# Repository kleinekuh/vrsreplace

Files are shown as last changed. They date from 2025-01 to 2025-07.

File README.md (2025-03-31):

# VRS Replace
This „simple“ project (circuit & software) is a replacement for my old Vaillant VRS auroMATIC 560 thermal solar control. Other VRS auroMATIC systems operating with VR10 / VR11 sensors, should also work. Furhter it's possible using the control for warm water heating only (C1/C2).

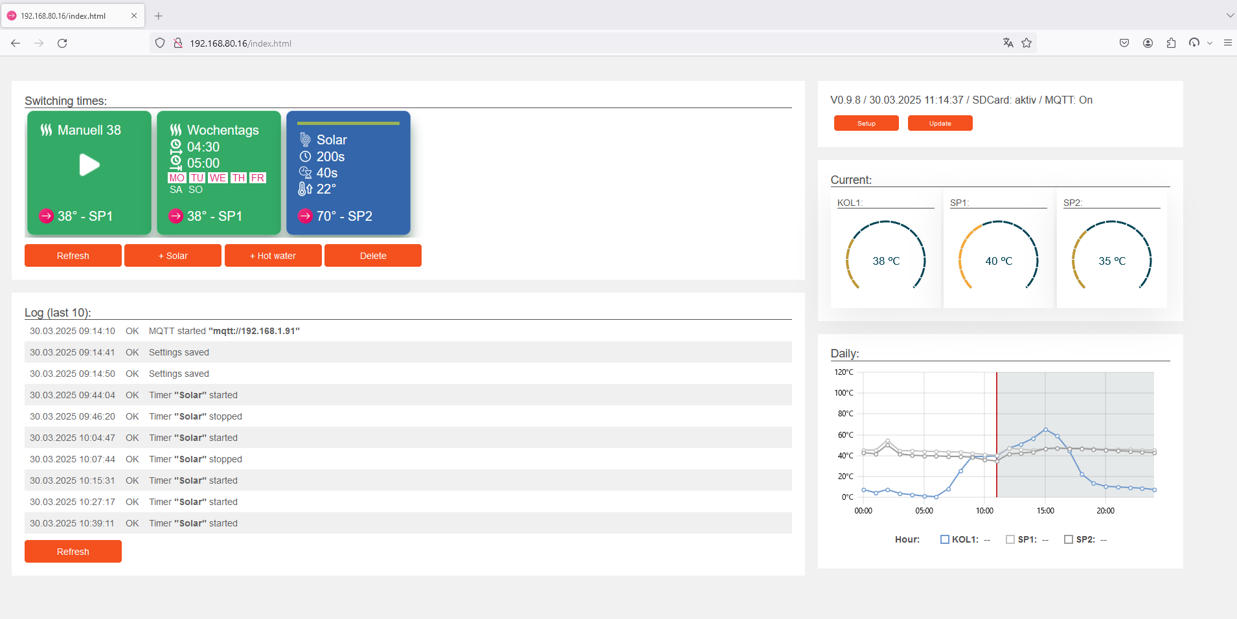
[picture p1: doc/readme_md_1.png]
main index html


> [!CAUTION]
> The circuit makes use of high voltage (240V). If you are not firm what this mean, don't do that and ask somebody for help.
>
>  The whole system is designed running behind your own firewall. On January 2025 there is no security layer or any auth mechanism implemented. Anybody with access to your network/system is able changing timer-programs or uploading new firmware.
>
> If you use this project inside an apartment building keep in mind that the DSGVO could be relevant.
>
> I spend a lot of time measuring right „ADC to Resistor“ values before i got the information that the actual used temperature sensors (VR10/11) are susceptible by environmental influences. The heating engineers at the time (year 2008) forgot using a shielded cable. This is really funny if the sensor cables placed near to a high voltage once.
>
> I am not responsible for any damages or a correct working.

## Why this project?
* Usage from my iPad
* One click warm-water heating
* Store temperature log on SD-Card
* Keep the existing tempsensors (VR 10 / VR 11)
* REST
* Don’t want to spend a lot of money. My heating engineer asked for such functionality around 1500 bucks. Further I had to drop my old BlackBerry and order a new mobile. Cheaper solutions require changing temperature sensors which implies rental of a scaffold for reaching the roof.
* Make things a little bit easier
* Every cubic meter of gas saved is good for the environment

## Solved issues / problems
* ESP – ADC’s in combination with resistor based temperature sensors → See „Usage /Installation“
* ESPAsyncWebServer → Replaced by PsychicHttp

## Usage / Installation:
1. Create the following folders on your SD-Card (FAT32):
„/webserver“ (if you want to load html, js and css from SD-Card)
„/log“
„/sensordata“

2. System operates with predefined LUT-Values. Everybody who already tried calculating resistor values would known that ESP’s have some room for improvement. For that reason you should generate your own LUT Value Table(s). You can use the solution from „e-thinkers“ (https://github.com/e-tinkers/esp32-adc-calibrate) or a more precisely solution from „Kveri“ (https://github.com/Kveri/esp32-adc-calibrate). The outputs must be converted to a row based „integer“ table. Each row representing the calculated int value. Make sure the output contains 4096 rows. If not, add a 0 as first line and no headers.

3. Copy your generated lut file to your sd card inside the folder „/sensordata“. A single file for each pin is required. Naming convention „lut_PIN_.txt“. You can use my provided files „lut36.txt“, „lut39.txt“ and „lut34.txt“ but i believe an own generated file is more precise.

4. Copy pregenerated sensorfiles vrs10.txt and vrs11.txt into the same „/sensordata“ folder.
Remark:
Both files are average values. This values had been measured on 8 different ESP’s with a physical resistance decade. Resistor values are based by the vendor documentation for my old VRS auroMATIC 560 (guide „Für den Betreiber/für den Fachhandwerker Bedienungs- und Installationsanleitung auroMATIC 560“ page 26).

5. Copy the *.html, mainall.js.gz and main.css.gz files into folder „/webserver“. Only required if you want to serve these files from your SD-Card.
Remark:
The ESP’s webserver are not really able dealing with a bunch of files. For that case i put all the relevant content like icons, external JS Libs and external defined CSS formating into one single file and did a gzip compression afterwards. For performance reasons these content had been placed inside *.h files for direct delivering it without file reading. Keep in mind if you want to do any changes on the HTML-Side. ;-)

6. Bring the bin(s) to your ESP or compile it by yourself.
Homekit libraries already included. This means that the partition scheme has to be changed. For that case you need „minimal SPIFFS (1.9MB APP with OTA/190KB SPIFFS)“

Installation with ESP32 FLASH DOWNLOAD TOOL (used version v3.9.8)

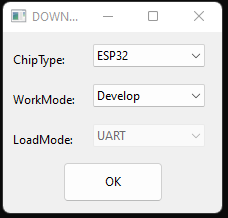
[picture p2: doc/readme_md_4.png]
Flashtool start dialog


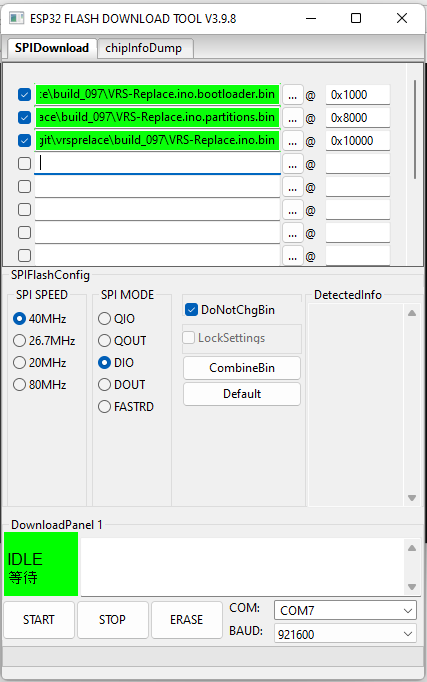
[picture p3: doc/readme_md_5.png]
Flashtool main dialog


| Bin-File | Address |
| :--- | :--- |
| VRS-Replace.ino.bootloader.bin | 0x1000 |
| VRS-Replace.ino.partitions.bin | 0x8000 |
| VRS-Replace.ino.bin | 0x10000 |

7. System should now started in AP Mode with the ssid VRS-Replace. Password „12345678“

## Configuration / Administration
* [Documentation "Configuration & Administration"](https://github.com/kleinekuh/vrsreplace/blob/main/doc/admin.md)
* [Documentation "REST"](https://github.com/kleinekuh/vrsreplace/blob/main/doc/rest.md)
* [Documentation "MQTT"](https://github.com/kleinekuh/vrsreplace/blob/main/doc/mqtt.md)
* [Documentation "Prometheus metrics"](https://github.com/kleinekuh/vrsreplace/blob/main/doc/metrics.md)

## Circuit / Layout
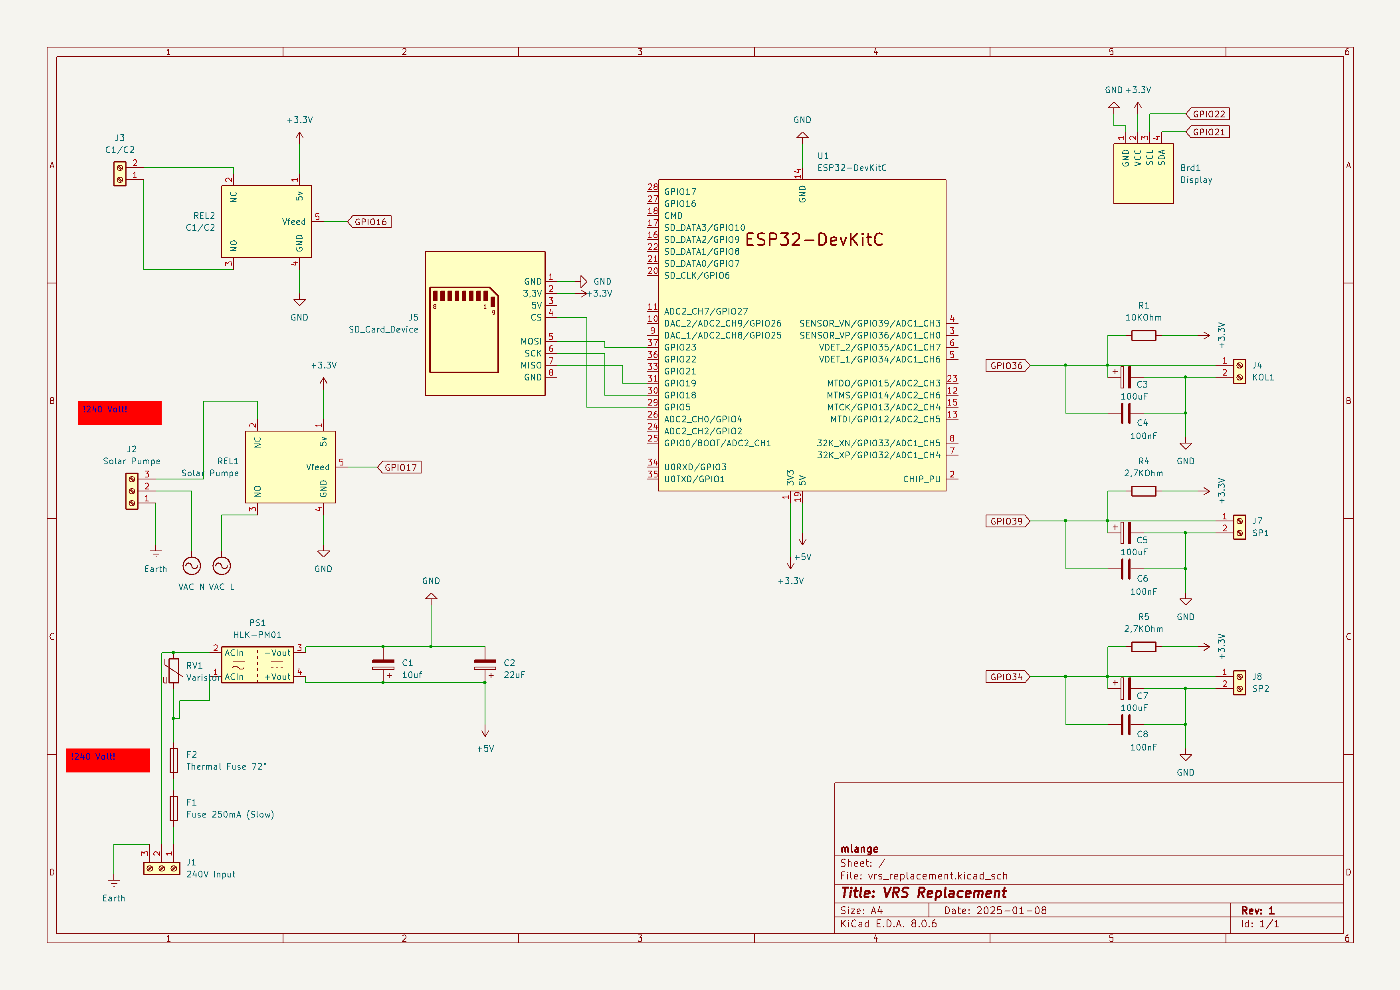
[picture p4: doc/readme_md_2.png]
circuit layout


## Used Parts
| Number | Part |
| --- | :--- |
| 1 | ESP32 DevKit C (see picture) |
| 1 | SD Card Module |
| 1 | 0,96‘‘ I2C Display (not required but nice) |
| 2 | Relays Boards |
| 2 | Screw Terminal (3 Connectors) |
| 4 | Screw Terminal (2 Connectors) |
| 1 | Varistor |
| 1 | Thermal Fuse 72°C |
| 1 | Fuse Slow 250mA |
| 1 | Fuse Holder |
| 1 | 10uF capacitor |
| 1 | 22uF capacitor |
| 3 | 100nF capacitors |
| 3 | 100uF capacitors |
| 2 | 2,7KOhm resistors |
| 1 | 10KOhm resistor |
| 1 | HLK-PM01 AC DC 220V on board power supply |

Layout of used ESP:
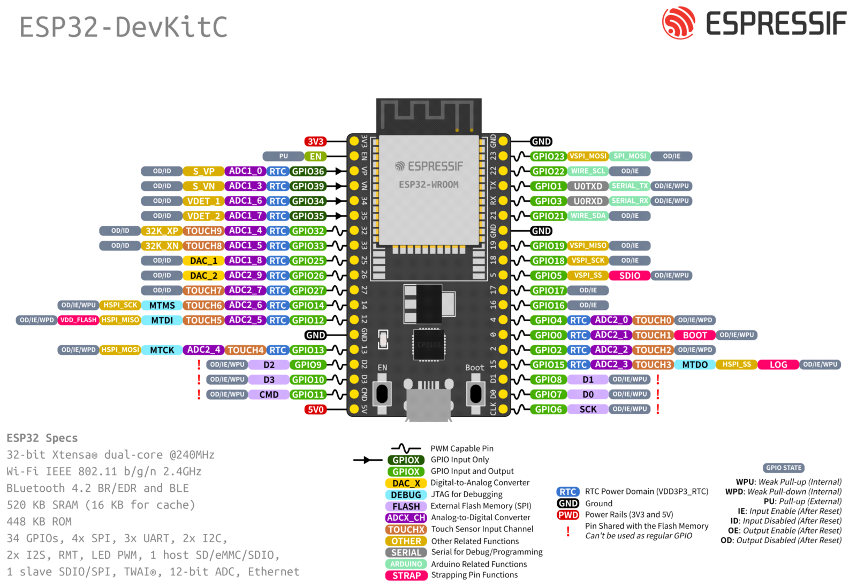
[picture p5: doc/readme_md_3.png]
layout used esp


Since November 2024 in use

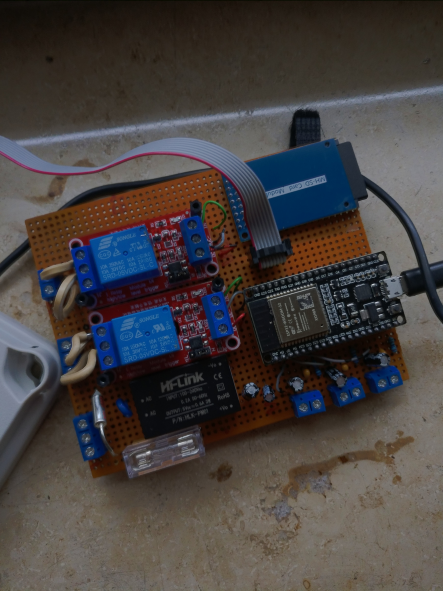
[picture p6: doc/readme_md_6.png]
assembled circuit


## Future:
- Ethernet Interface
- ~~Homekit integration~~ Removed. Should be possible over MQTT solution like openhab, ...
- ~~MQTT~~ Added 0.9.8
- ~~Multilanguage with different timezones (actually you have to change the HTML & JS Code)~~ Added 0.9.8 en/de
- User/Pass
- HTTP/S
- Dynamic timer programs
	- Waterheating should be ready at HH:mm
	- Based on weather forecast, „Legionella Program“ should start weekly at Day/Hour -> 60°C
- Changing the whole development environment
- I am not really happy with the WebFrontend. It works and the performance is Ok, but sometimes a more fancier FE would be nice.
- Changing the js charts lib. Especially the line chart is not easy to handle.
- ~~Add validation rules on the input elements.~~ Added 0.9.8
- Support for circulation pump. Actually there is no installed in our house.
- Solar yield calculation
- Adding a working mDNS solution. Until now add the given IP to your router.

## History:

Actual version: 0.9.8

- Support for MQTT
- Reduced Heap memory usage
- Different languages (en/de)
- Added metrics endpoint for Prometheus Logging.
- Different European Timezones

Version: 0.9.7
- Initial Version

## Additional Software
VRS Replace uses the following OpenSource components:
* HTMX
https://htmx.org/
https://github.com/bigskysoftware/htmx

* svg-gauge
https://github.com/naikus/svg-gauge

* uPlot
https://github.com/leeoniya/uPlot

* PsychicHttp
https://github.com/hoeken/PsychicHttp

## License
Sourcecode, Documentation and Circuit-Plan are under GPL V3.

## Thanks
Big thanks to my neighbor Lorenz. He brought me to the idea using a linear interpolation for calculating missing temp values. Without his input i would still discussing this topic with his father, a mathematician.
To my partner. Everyboy knows that hair washing without warm water isn’t funny.

## Comments
The source code is deliberate undocumented. I am not a friend of AI generated code. Any questions → Ask!

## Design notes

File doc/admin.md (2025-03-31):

# VRS-Replace Configuration / Administration

Without any configuration the system would start in AP-mode. Your WiFi-device (mobile, tablet, pc) should show a network named „VRS-Replace“. After connecting with the password „12345678“ you can reach the configuration page by entering the IP: http://192.168.4.1 inside your browser.

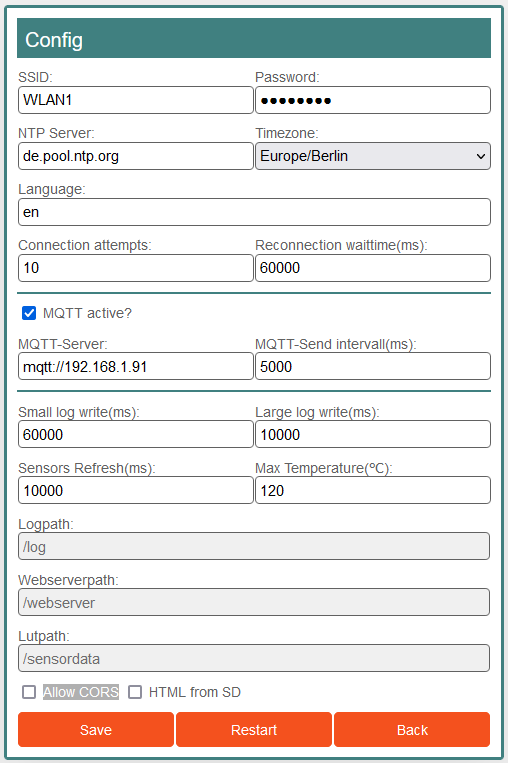
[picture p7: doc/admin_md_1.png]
Config dialog


This menu could also be reached hitting the button "Setup"

| Parameter | Change requires restart | Description |
| :--- | :--- | :--- |
| SSID: | x | SSID of the WiFi Network |
| Password: | x | Password for WiFi Network |
| NTP Server: |  | IP or domain of the NTP-Server |
| Timezone: |  | Selection of different European timezones. For Germany select: Europe/Berlin |
| Language: |  | Supported languages de (default), en |
| Connection attempts: |  | Number of connection retries before starting in AP-Mode |
| Reconnection waittime(ms): |  | Waittime in ms before trying next WiFi reconnect |
| MQTT active? |  | Activates MQTT |
| MQTT-Server: |  | The URL for the MQTT Server. "mqtt://" must be added on the URL |
| MQTT-Send intervall(ms): |  | Interval(ms) sending MQTT messages |
| Small log write(ms): |  | Time in ms for writing small temperature log (see /downloadtemperaturelog) |
| Large log write(ms): |  | Time in ms for writing large temperature log (see /downloadtemperaturelog) |
| Sensors Refresh(ms): |  | Time in ms for refreshing the temperature sensors |
| Max Temperature(°C): |  | Max Temperature of the collector sensor, before switching off |
| Logpath: |  | Folder on SD-Card for the Log-Files |
| Webserverpath: |  | Folder on SD-Card where the WebServer retrieves JS/CSS and HTML Files |
| Lutpath: |  | Folder on SD-Card for the LUT predefined values |
| Allow CORS | x | Allows CORS Headers. Important for own Webpage development. |
| HTML from SD |  | If activated the webserver delivers HTML’s, JS and CSS directly from SD-Card. This files have to be exist before. |

After entering correct parameters, hit „Save“ and restart „Restart“. If WiFi connection will not work, the system will coming back in AP-mode after Connection attempts * Reconnection waittime(ms)).

With correct connection credentials the system would now connect to your WiFi and you are able adding timer programs for solar and warm water heating. The IP depends on your WiFi DHCP setup. If display is used the assigned IP would be shown.

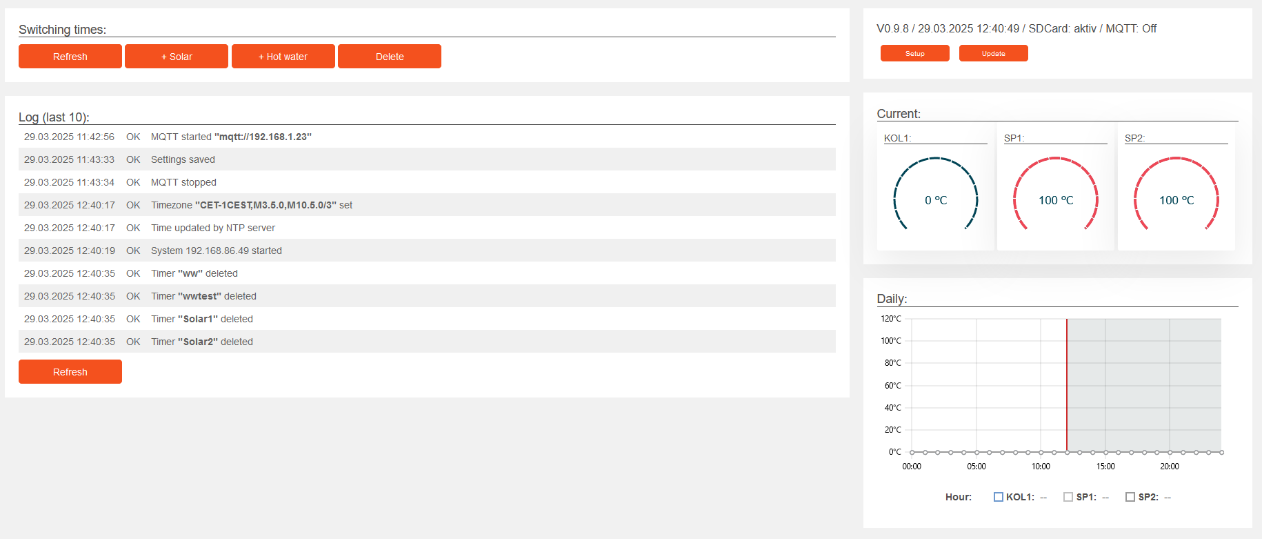
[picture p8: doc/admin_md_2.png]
dialog main


## Timer for solarpump
Hitting "+ Solar" will opening a dialog for a new solar pump timer program:

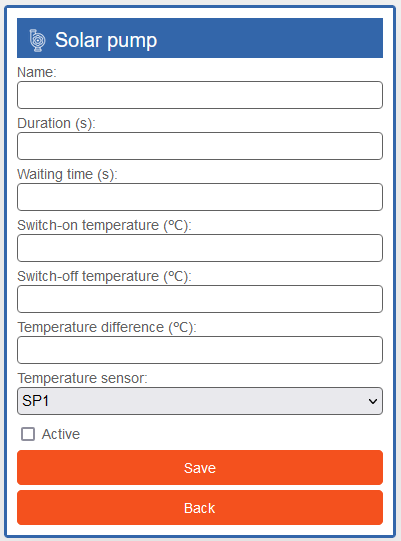
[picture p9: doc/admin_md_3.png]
dialog solarpump


| Parameters | Description |
| :--- | :--- |
| Name: | Name of this timer |
| Duration (s): | Time in seconds how long the timer should run |
| Waiting time (s): | Time in seconds how long the timer should wait |
| Switch-on temperature (℃): | Which temperature (Kol1) should be reached, before activating this timer. |
| Switch-off temperature (℃): | Target temperature before stopping the timer. Temperature is based on Temperature sensor“ selection. |
| Temperature difference (℃): | Temperature difference Kol1 ↔ Temperature sensor“ for starting the solar pump. If temperature is lower then the given value and target is not reached, timer goes into wait mode. |
| Temperature sensor: | Relevant sensor for measuring target temperature Sp1, Sp2 or Average|
| Activ | Timer program active or not. |

## Timer for warmwater heating
Hitting "+ Hot water" will opening a dialog for a new warm water heating timer program:

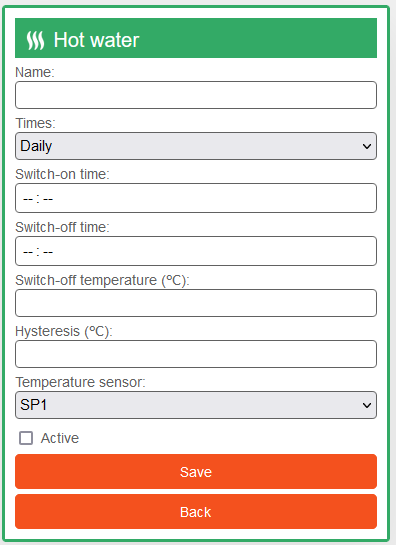
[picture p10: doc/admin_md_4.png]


| Parameters | available inside timerprogam | Description |
| :--- | :--- | :--- |
| Name: | All | Name of this timer |
| Times: | All | Selection for different timer program: - Daily = every day - Weekdays = Only at day selection - Manualy = Running at single click |
| MO, TU, WE, TH, FR, SA, SO | Weekdays | Timer should run at this weekday(s) |
| Switch-on time: | Daily / Weekdays | Timer should start at HH24:mm |
| Switch-off time: | Daily / Weekdays | Timer should end at HH24:mm |
| Switch-off temperature (℃): | All | Target temperature before stopping the timer. Temperature is based on „Temperature sensor“ selection. |
| Hysteresis (℃): | Daily / Weekdays | If temperature but end time had not been reached, timer goes into waiting and restarts if target temperature goes under this value. |
| Temperature sensor: | All | Relevant sensor for measuring target temperature Sp1, Sp2 or Average. |
| Activ | All | Timer program active or not. |

## Section "Switching times"
Shows the created timer programs. If timer is running a red bar is shown inside the program. If bar becomes yellow timer is in waiting state.

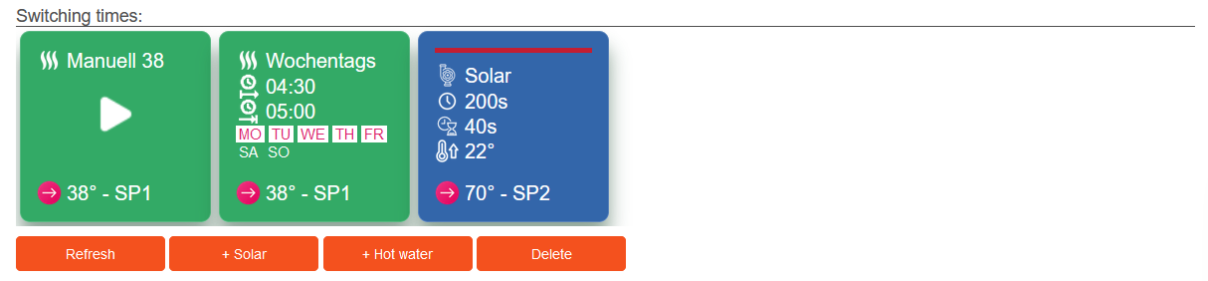
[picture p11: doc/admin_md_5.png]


| Button(s) | Description |
| :--- | :--- |
| Refresh | Refreshes the list of timer programs. |
| + Solar | Adds a new program for the solar pump. |
| + Hot water | Adds a new program for warm water heating. |
| Delete | Highlighted timer programs (single click / red frame) got deleted without any warning. |

Double click or long touch on single timer will opening program for changing.

## Section "Log (last 10):"
Lists the last 10 protocol entries.

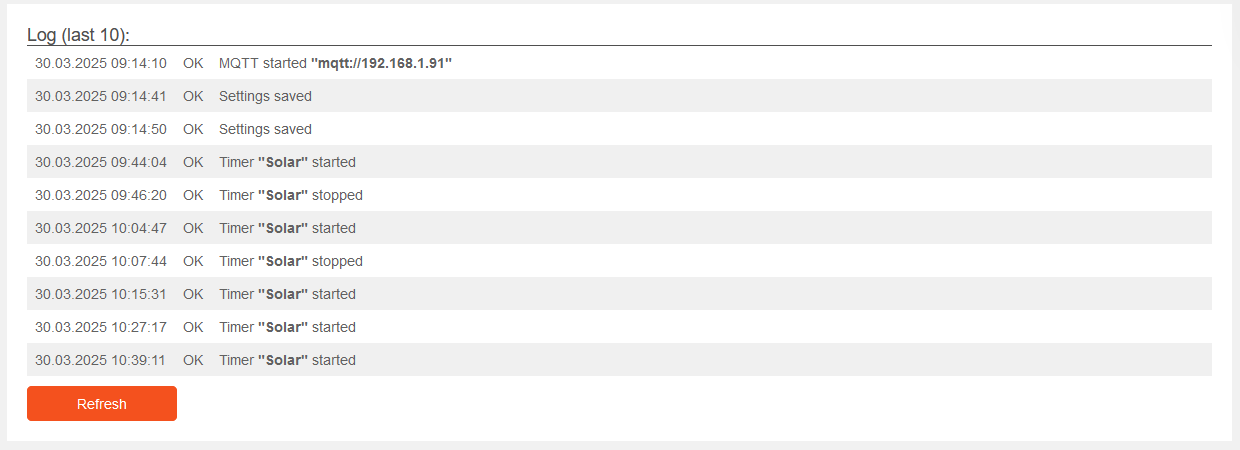
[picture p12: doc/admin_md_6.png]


| Button(s) | Description |
| :--- | :--- |
| Refresh | Refreshes the log entries list. |

## Section "State"
Shows actual information about the system: Version, date time, status of the SD-Card and if MQTT is on or off

dialog heating

| Button(s) | Description |
| :--- | :--- |
| Setup | Opens the configuration window. |
| Update | Opens the page for updating the system. |

## Section "Current"
Shows the current temperature for each sensor.

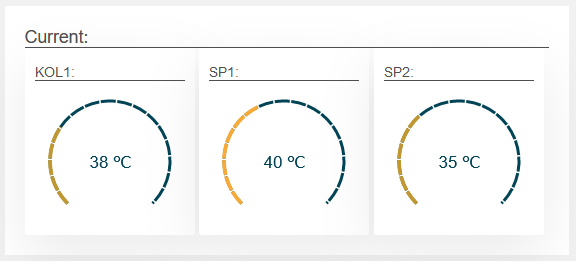
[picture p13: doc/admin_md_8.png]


## Section "Daily"
Shows temperature history for today and previous day. The red line symbolizes the actual hour. The grayed part shows temperature from previous day.

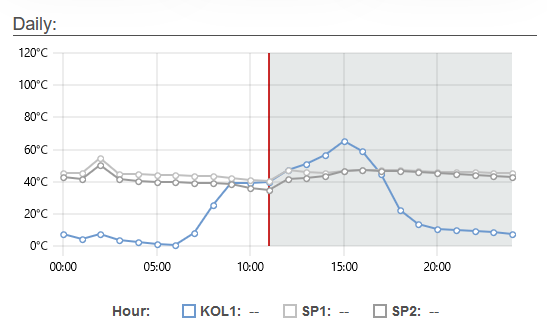
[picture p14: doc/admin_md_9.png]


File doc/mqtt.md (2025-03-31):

# VRS Replace - MQTT

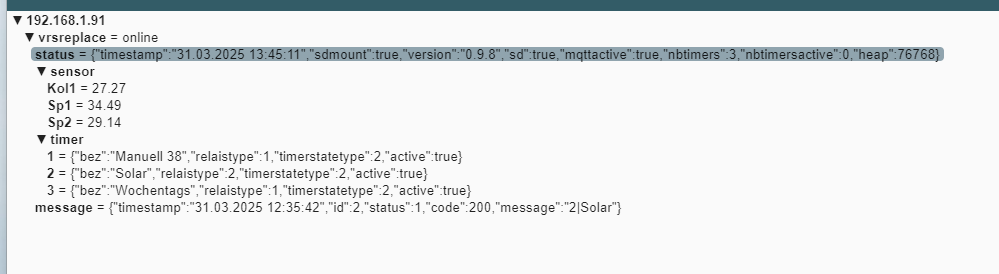
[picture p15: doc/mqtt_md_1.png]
MQTT Explorer VRS Replace topics


Readable Topics

| Topic: | Type: | Description: |
| :--- | :--- | :--- |
| /vrsreplace | string | Current information about the general system status. This topic includes the LWT. |
| /vrsreplace/status | json | Informations from the system. Same content as from the REST service "/status" |
| /vrsreplace/sensor/[Sensor] | double | Actual measured sensor temperature (Kol1, Sp1, Sp2)  |
| /vrsreplace/timer/[Timer ID] | json | Status of the defined timers. |
| /vrsreplace/message | string | Last published log message. |

Writable Topics

| Topic: | Type: | Description: |
| :--- | :--- | :--- |
| /vrsreplace/timer/[Timer ID]/cmd | string | All timers could be activated and deactivated by sending "activate" or "deactivate" as message. Timers with relaistype=3 (Timerprogram Manually) are able to "start" and "stop" sending the equivalent message. |

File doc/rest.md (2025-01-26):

# VRS Replace - REST API

The frontend communicates directly with the backed API by calling any URL’s in combination with some parameters. Results are normally send back as JSON resultset.

My environment has an assigned IP 192.168.80.16

## /status
Delivers information about the actual system state.
| Input: | Type: |  |
| :--- | :--- | :--- |
| NONE |  |  |
| **Output:** |  |  |
| timestamp | string | Timestamp with the format dd.MM.yyyy HH24:mm:ss |
| sdmount | bool | SD Card mounted |
| version | double | The software version |
| sd | bool  | SD Interface exists |
| nbtimers | int | Number of defined timers |
| heap | int | Size of current available heap memory (bytes) |

## /log
Delivers the last 10 system-logentries
| Input: | Type: |  |
| :--- | :--- | :--- |
| NONE |  |  |
| **Output:** | Array[10] |  |
| id | int | Increasing INT-Value |
| priocode | int | Priority of this entry |
| date | int | Datestamp Format:yyyyMMdd |
| time | int | Timestamp Format:H24mmss !Leading zero is terminated! |
| code | int | Message Code → Struct LogStatusCode |
| message | string | Associated Message Example: code=201 / message=5!morgens Translated: Timer with id=5 and name=morgens had been stopped |

## /downloadtemperaturelog
Download logfile with temperature values. Logfile exists in two different formats (small and full).
| Input: | Type: |  |
| :--- | :--- | :--- |
| logfile | int | Date for the logfile to download. Format: yyyyMMdd |
| type | string | small / full |
| **Output:** | Start HTTP Download |  |
| NONE |  |  |

### CSV Document small
| Column: | Type: |  |
| :--- | :--- | :--- |
| 1 | int | Temperature sensor / 0=Kol1; 1=Sp1; 2=Sp2 |
| 2-25 | int | Max Temperatures full hour |
| 26-49 | int | Min Temperatures full hour |

### CSV Document full
| Column: | Type: |  |
| :--- | :--- | :--- |
| 1 | int | Datestamp format yyyyMMdd |
| 2 | string | Timestamp format: HH24mmss |
| 3 | int | Id of active heattimer |
| 4 | int | Id of active solartimer |
| 5 | int | Id of active circulationtimer (Currently not used) |
| 6 | string | Name of the Tempsensor (Kol1, Sp1, Sp2) |
| 7 | int | Id of the Tempsensor |
| 8 | double | Actual temperature |
| 9 | double | Max temperature (per day) |
| 10 | double | Min temperature (per day) |

## /temperature
Retrieves the actual temperatures as JSON Array
| Input: | Type: |  |
| :--- | :--- | :--- |
| NONE |  |  |
| **Output:** | Array[3] |  |
| bez | string | Name of the Tempsensor |
| deviceid | int | Id of the sensor Kol1=0 / Sp1 = 1 / Sp2 = 2 |
| sensortype | int | Sensortype VR10 = 1 / VR11=2 |
| Ta | double | Actual temperature |
| TaAvg | double | Avg temperature (depends config sensorAvgTemperatureCalcSize) |
| TaMin | double | Temperature Min (per hour) |
| TaMax | double | Temperature Max (per hour) |
| TaMinH | double Array[24] | Array with min temperatures per hour |
| TaMaxH | double Array[24] | Array with max temperatures per hour |
| TaMinY | double Array[24] | Array with min temperatures per hour / previous day |
| TaMaxY | double Array[24] | Array with max temperatures per hour / previous day |

## /config
Returns the actual configuration values
| Input: | Type: |  |
| :--- | :--- | :--- |
| NONE |  |  |
| **Output:** |  |  |
| ssid | string | SSID of the used WiFi Network |
| password | string | Always *** |
| ntpserver | string | IP or domain of the NTP-Server |
| lutpath | string | Folder on SD-Card for the LUT predefined values |
| logpath | string | Folder on SD-Card for the Log-Files |
| webserverpath | string | Folder on SD-Card where the WebServer retrieves JS/CSS and HTML Files |
| temperaturesrt | int | Time in ms for refreshing the tempsensors |
| temperaturelwt | int | Time in ms for writing large temperature log (see /downloadtemperaturelog) |
| temperatureswt | int | Time in ms for writing small temperature log (see /downloadtemperaturelog) |
| wificonnectionretries | int | Number of connection retries before starting in AP-Mode |
| wifireconnectinterval | int | Waittime in ms before trying next WiFi reconnect |
| maxtemperature | int | Max Temperature of the solar storage unit |
| version | string | Installed Version |
| allowcors | bool | CORS Header set |
| deliverfromsd | bool | Load HTML’s, JS and CSS from SD-Card |

## /system
Allows some system change by adding one of the following parameter to the URL.
| Input: | Type: |  |
| :--- | :--- | :--- |
| reboot | string | Reboots the system |
| ntp | string | Recalls the datetime from configured NTP-Server |
| eraseconfig | string | Deletes the whole config and starts the system in AP-Mode |
| **Output:** | JSON Status |  |
| timestamp | string | DateTimestamp format dd.MM.yyyy HH24:mm:ss |
| id | int | Id of the timer. If function not relevant to timer, -1 is returned |
| status | int | 1=Ok / 2=Error |
| code | int | Statuscode see enum LogStatusCode |

Example:
```
URL: 
	http://<IP>/system?ntp → Recalls the datetime from configured NTP-Server.
Return:
	{"timestamp":"05.01.2025 16:43:37","id":-1,"status":1,"code":112}
	Status: 1 = Ok
	Code: 112 = System NTP-Time refreshed
```

## /changeconfig
Changing the existing config parameters. Changing SSID and/or Password requires a reboot of the system. 
| Input: | Type: |  |
| :--- | :--- | :--- |
| config | JSON document |  |
| **Input JSON document** |  |
| ssid | string | SSID of the used WiFi Network |
| password | string | Password for the WiFi Network |
| ntpserver | string | IP or Domain for the NTP-Server |
| temperaturesrt | int | Time in ms for refreshing the tempsensors |
| temperaturelwt | int | Time in ms for writing large temperature log (see /downloadtemperaturelog) |
| temperatureswt | int | Time in ms for writing small temperature log (see /downloadtemperaturelog) |
| wificonnectionretries | int | Number of connection retries before starting in AP-Mode |
| wifireconnectinterval | int | Waittime in ms before trying next WiFi reconnect |
| maxtemperature | int | Max Temperature of the solar storage unit |
| **Output:** | JSON Status |  |
| timestamp | string | DateTimestamp format dd.MM.yyyy HH24:mm:ss |
| id | int | Id of the timer. If function not relevant to timer, -1 is returned |
| status | int | 1=Ok / 2=Error |
| code | int | Statuscode see enum LogStatusCode |

## /timer
Returns the timer by providing a valid timer id. Return structure is similar to timerlist. If timer could not be found a status document would be send.
| Input: | Type: | Timer Program (s): | Relays: |  |
| :--- | :--- | :--- | :--- | :--- |
| id | int | All | All | ID of the timer |
| **Output:** | JSON Document |  |  |  | 
| pos | string | All | All |  |
| id | int | All | All | Unique id of the timer.  |
| bez | string | All | All | Given Name of this timer |
| gpiopin | int | All | All | ESP Pin used for relays |
| relais | int | All |  | Assigned relays to this timer 1=Heat, 2=Solar, 3=Circulation |
| time_on | int | 1,2 | 1 | Starttime format H24mmss |
| time_off | int | 1,2 | 1 | Endtime format H24mmss |
| weekdays | int Array[7] | 2 | 1 | Weekdays when the timer should be active. |
| running_period | int |  | 2 | Time in ms timer should run (gpio=high) |
| waiting_period | int |  | 2 | Time in ms timer should wait before switching to run (gpio=low) |
| timer_program | int |  | 1 | Type of this Timer 1=Daily, 2=Weekdays, 3=Per request, 4=Dynamic |
| temperature_on | int |  | 2 | Kol1 Temperature for starting this timer |
| temperature_off | int | 1,2,3 | 1,2 | Temperature for stopping this timer |
| tempsensor | int | All | All | Relevant sensor for measuring target temperature None = 0, Sp1 = 1, Sp2 = 2, Avg_Sp1_Sp2 = 3, Kol1 = 4 |
| temperature_difference | int |  | 2 | Temperature difference Kol1 ↔ tempsensor, for starting solar pump |
| hysteresis | int | 1,2 | 1 | Temperature difference for running Heat-Timer before restarting warm water heating. |
| active | bool | All | All | Activated = True, Deactivated = False |
| state | bool | All | All | Running state Running = true |
| timerstatetype | int | All | All | Current Timerstate 1 = On, 2 = Off, 3 = Wait |
| runnings | int | All | All | How often this timer had been running |
| waitings | int | All | All | How often this timer are set to wait state |
| laststartdate | int | All | All | Last startdate of this timer format: yyyyMMdd |
| laststarttime | int | All | All | Last starttime of this timer format: H24mmss |
| publishhomekit  | bool | 3 | 1 | Should this timer published to homekit (future) |
| avgtempincreasepermin | int | 1,2,3 | 1,2 | Average temperature increasement per minute for this timer (future) |

## /timerchange
Returns the timer by providing a valid timer id. Return structure is similar to timerlist. If timer could not be found a status document would be send.
| Input: | Type: | Timer Program (s): | Relays: |  |
| :--- | :--- | :--- | :--- | :--- |
| timer | JSON Document | All | All | |
| **Input JSON Document** |  |  |  |  | 
| id | int | All | All | Unique id of the timer. -1 = Create new timer |
| bez | string | All | All | Given Name of this timer |
| gpiopin | int | All | All | ESP Pin used for relays |
| relais | int | All |  | Assigned relays to this timer 1=Heat, 2=Solar, 3=Circulation |
| time_on | int | 1,2 | 1 | Starttime format H24mmss |
| time_off | int | 1,2 | 1 | Endtime format H24mmss |
| weekdays | int Array[7] | 2 | 1 | Weekdays when the timer should be active. |
| running_period | int |  | 2 | Time in ms timer should run (gpio=high) |
| waiting_period | int |  | 2 | Time in ms timer should wait before switching to run (gpio=low) |
| timer_program | int |  | 1 | Type of this Timer 1=Daily, 2=Weekdays, 3=Per request, 4=Dynamic |
| temperature_on | int |  | 2 | Kol1 Temperature for starting this timer |
| temperature_off | int | 1,2,3 | 1,2 | Temperature for stopping this timer |
| tempsensor | int | All | All | Relevant sensor for measuring target temperature None = 0, Sp1 = 1, Sp2 = 2, Avg_Sp1_Sp2 = 3, Kol1 = 4 |
| temperature_difference | int |  | 2 | Temperature difference Kol1 ↔ tempsensor, for starting solar pump |
| hysteresis | int | 1,2 | 1 | Temperature difference for running Heat-Timer before restarting warm water heating. |
| active | bool | All | All | Activated = True, Deactivated = False |
| **Output:** | JSON Status |  |
| timestamp | string | | | DateTimestamp format dd.MM.yyyy HH24:mm:ss |
| id | int | | | Id of the timer. If function not relevant to timer, -1 is returned |
| status | int | | | 1=Ok / 2=Error |
| code | int | | | Statuscode see enum LogStatusCode |

## /timerdelete
Deletes exiting timer(s) by providing the
| Input: | Type: |  |
| :--- | :--- | :--- |
| timers | JSON Array | JSON Array with timer id(s) to delete |
| **Output:** | JSON Status |  |
| timestamp | string | DateTimestamp format dd.MM.yyyy HH24:mm:ss |
| id | int | Id of the timer. If function not relevant to timer, -1 is returned |
| status | int | 1=Ok / 2=Error |
| code | int | Statuscode see enum LogStatusCode |

## /timerdeleteall
Deletes all existing timers. Before deletion all timers will be stopped and deactivated.
| Input: | Type: |  |
| :--- | :--- | :--- |
| NONE |  |  |
| **Output:** | JSON Status |  |
| timestamp | string | DateTimestamp format dd.MM.yyyy HH24:mm:ss |
| id | int | Id of the timer. If function not relevant to timer, -1 is returned |
| status | int | 1=Ok / 2=Error |
| code | int | Statuscode see enum LogStatusCode |

## /timerlist
Returns a list with the existing timers.
| Input: | Type: | Timer Program (s): | Relays: |  |
| :--- | :--- | :--- | :--- | :--- |
| NONE |  |  |  |  |
| **Output:** | JSON Array |  |  |  | 
| pos | string | All | All |  |
| id | int | All | All | Unique id of the timer.  |
| bez | string | All | All | Given Name of this timer |
| gpiopin | int | All | All | ESP Pin used for relays |
| relais | int | All |  | Assigned relays to this timer 1=Heat, 2=Solar, 3=Circulation |
| time_on | int | 1,2 | 1 | Starttime format H24mmss |
| time_off | int | 1,2 | 1 | Endtime format H24mmss |
| weekdays | int Array[7] | 2 | 1 | Weekdays when the timer should be active. |
| running_period | int |  | 2 | Time in ms timer should run (gpio=high) |
| waiting_period | int |  | 2 | Time in ms timer should wait before switching to run (gpio=low) |
| timer_program | int |  | 1 | Type of this Timer 1=Daily, 2=Weekdays, 3=Per request, 4=Dynamic |
| temperature_on | int |  | 2 | Kol1 Temperature for starting this timer |
| temperature_off | int | 1,2,3 | 1,2 | Temperature for stopping this timer |
| tempsensor | int | All | All | Relevant sensor for measuring target temperature None = 0, Sp1 = 1, Sp2 = 2, Avg_Sp1_Sp2 = 3, Kol1 = 4 |
| temperature_difference | int |  | 2 | Temperature difference Kol1 ↔ tempsensor, for starting solar pump |
| hysteresis | int | 1,2 | 1 | Temperature difference for running Heat-Timer before restarting warm water heating. |
| active | bool | All | All | Activated = True, Deactivated = False |
| state | bool | All | All | Running state Running = true |
| timerstatetype | int | All | All | Current Timerstate 1 = On, 2 = Off, 3 = Wait |
| runnings | int | All | All | How often this timer had been running |
| waitings | int | All | All | How often this timer are set to wait state |
| laststartdate | int | All | All | Last startdate of this timer format: yyyyMMdd |
| laststarttime | int | All | All | Last starttime of this timer format: H24mmss |
| publishhomekit  | bool | 3 | 1 | Should this timer published to homekit (future) |
| avgtempincreasepermin | int | 1,2,3 | 1,2 | Average temperature increasement per minute for this timer (future) |

## /timerstart
Starts the timer by providing the timer id.
| Input: | Type: |  |
| :--- | :--- | :--- |
| id | int | Id of the timer to start |
| **Output:** | JSON Status |  |
| timestamp | string | DateTimestamp format dd.MM.yyyy HH24:mm:ss |
| id | int | Id of the timer. If function not relevant to timer, -1 is returned |
| status | int | 1=Ok / 2=Error |
| code | int | Statuscode see enum LogStatusCode |

## /timerstop
Stops the timer by providing the timer id.
| Input: | Type: |  |
| :--- | :--- | :--- |
| id | int | Id of the timer to stop |
| **Output:** | JSON Status |  |
| timestamp | string | DateTimestamp format dd.MM.yyyy HH24:mm:ss |
| id | int | Id of the timer. If function not relevant to timer, -1 is returned |
| status | int | 1=Ok / 2=Error |
| code | int | Statuscode see enum LogStatusCode |

## /testrelay
Test relays by setting the relevant gpio high or low.
| Input: | Type: |  |
| :--- | :--- | :--- |
| gpio | int | GPIO Pin for high/low activation. Current GPIO 16 = HEAT, GPIO 17 = SOLAR_PUMP |
| onoff | int | On = 1 / Off = 0 |
| **Output:** | JSON Status |  |
| timestamp | string | DateTimestamp format dd.MM.yyyy HH24:mm:ss |
| id | int | Id of the timer. If function not relevant to timer, -1 is returned |
| status | int | 1=Ok / 2=Error |
| code | int | Statuscode see enum LogStatusCode |

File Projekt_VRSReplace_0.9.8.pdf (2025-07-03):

# Projekt „Austausch einer bestehenden Thermischen Solarregelung kurz VRS Replace“

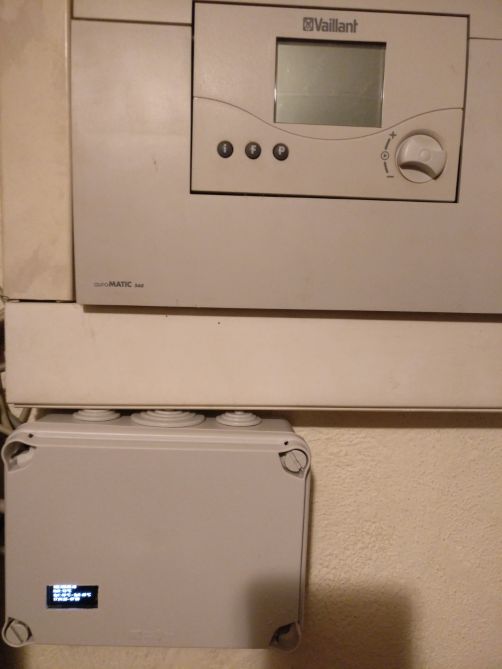
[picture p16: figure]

Oben Alt / unten Neu (seit November 2024)

# Hinweise / Disclaimer

- Die im Folgenden mögliche Schaltung arbeitet mit 240V!
- Es handelt sich hierbei um kein Breadboard Projekt!
- Sollten Begriffe wie „Duspol“, „Schutzleiter“, „Phase(n)“, „FI“ und „Neutralleiter“ Fremdworte sein, so bitte die Idee an eine mögliche Umsetzung direkt und komplett verwerfen!
- Sollte die Stromleitung zum bisherigen/zukünftigen/auszutauschenden Solar-Regler auch nicht komplett stromlos geschaltet werden können, bitte im Allgemeinen erst für eine korrekte Installation des bestehenden/auszutauschenden Systems sorgen!
- Das im Folgenden beschriebene Projekt, protokolliert im gewissen Umfang Temperaturdaten. Diese Daten könnten u.A. Rückschlüsse auf Gewohnheiten einzelner im Haushalt lebender Personen ermöglichen! Es ist daher nicht auszuschließen, dass bei Verwendung in vermieteten Wohnräumen die DSGVO zu berücksichtigen ist!
- In meinem/unseren Fall wurde von dem damaligen Heizungsmonteuren kein abgeschirmtes Kabel bei der Installation der Temperaturfühler verwendet. Bitte berücksichtigen!
- Stand April 2025 beinhaltet der mitgelieferte Code (Version 0.9.8) keinerlei Authentifizierungsmechanismen und auch keinerlei Verschlüsselungen (SSL). Der mögliche Betrieb sollte daher nur in einer abgesicherten Umgebung in Betracht gezogen werden!
- Bei der im Folgenden beschriebenen Umsetzung handelt der Autor rein aus privatem Interesse. Es werden daher keinerlei Garantien für eine korrekte Funktionsweise und/oder irgendwelche Schäden übernommen!
- Die beschriebene Umsetzung bezieht sich rein auf die beim Autor existierende Heizungsinstallation! Es gibt kein „Schwimmbad“, „nur zwei Kollektoren“, „keine Zirkulationspumpe“, „keine Umschaltventile“, „keinen Wärmemengenzähler“, … (siehe Heizungsinstallation)
- Dieses Dokument und der mit diesem Dokument veröffentlichte Quellcode bezieht sich derzeit einzig und allein auf die Version 0.9.8! Zukünftige Erweiterungen, Programmanpassungen, Änderungen, … werden vorrangig auf dem zugehörigen Github Repository (siehe Link github) veröffentlicht.
- Die Beschreibung und der Quellcode unterliegen der Open Source Lizenz GPLv3 (siehe Lizenz)

Seite 2
Projekt VRS-Replace / © M. Lange / https://github.com/kleinekuh/vrsreplace / GPL v3

## Inhaltsverzeichnis

Seite 3

# Beschreibung Allgemein / Warum

Dieses „einfache“ Projekt wurde dafür erdacht, die Funktionen eines Solar-Differenztemperaturreglers (hier VRS auroMATIC 560) abzubilden und einige Dinge zu verbessern. Neben der Steuerung der Solarpumpe, können auch beliebig viele Zeitprogramme für die Warmwasseraufbereitung hinterlegt werden, es erfolgt eine Protokollierung der einzelnen Messwerte direkt auf einer SD-Karte und das System ist mittels Webbrowser per Wi-Fi steuerbar. Ferner werden die bereits verbauten Temperatursensoren ( VR10 und VR11 ) weiterverwendet. Der Austausch durch PT1000 und/oder DS18B20 ist somit nicht notwendig und derzeit auch nicht vorgesehen.

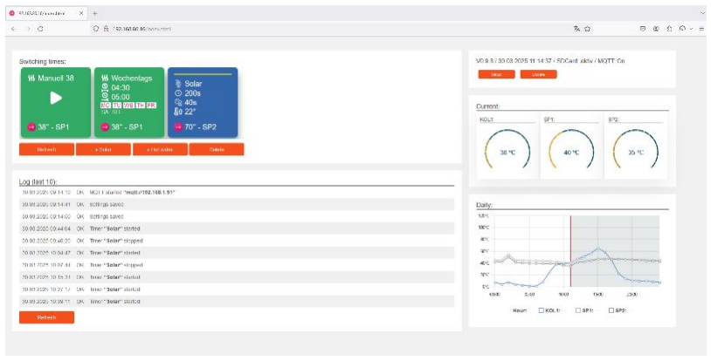
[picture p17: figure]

## Link github

Zusätzliche Informationen, sowie Binaries zukünftige Änderungen und Anpassungen können unter https://github.com/kleinekuh/vrsreplace abgerufen bzw. eingesehen werden.

## Heizungsinstallation

Unsere derzeitige Heizungsanlage besteht aus folgenden Komponenten.

Anzahl | Bezeichnung | Beschreibung
1 | VIH S 300 | Bivalenter Warmwasserspeicher für Solaranlagen
1 | VKK 226/2 | Gas-Brennwertkessel (Heizung und Warmwasser)
1 | auroMATIC 560 | Solardifferenzregler
1 | VR11 | Temperatursensor
2 | VR10 | Temperatursensor
2 | auroTHERM VFK 155 | Solar-Flachkollektoren
1 | WILO Yonos-PICO-STG | Solar-Umwälzpumpe

Wie unter „Hinweise / Disclaimer“ bereits erwähnt, besteht unser System aus keinen weiteren Komponenten. Es ist zwar eine Zirkulationsleitung vorhanden, allerdings ist hier keine entsp. Pumpe verbaut. Die projektspezifische Berücksichtigung einer Ansteuerung von Zirkulationspumpen wurde daher als nicht notwendig angenommen.

Seite 4

# Aufbau / Schaltplan

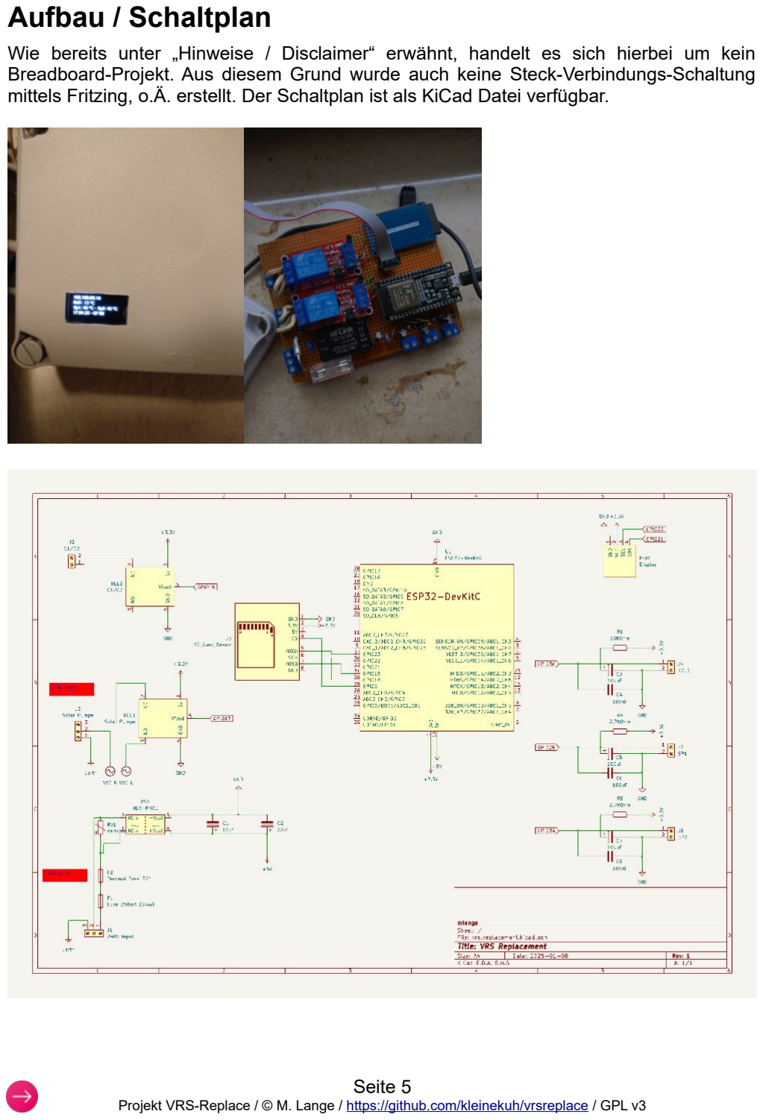
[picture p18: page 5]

Wie bereits unter „Hinweise / Disclaimer“ erwähnt, handelt es sich hierbei um kein Breadboard-Projekt. Aus diesem Grund wurde auch keine Steck-Verbindungs-Schaltung mittels Fritzing, o.Ä. erstellt. Der Schaltplan ist als KiCad Datei verfügbar.

Seite 5

## Bauteile

Folgende elektronischen Bauteile wurden für die Umsetzung verwendet.

Anzahl | Bauteile
1 | ESP32 DevKit C (siehe Bild)
1 | SD Card Modul
1 | 0,96‘‘ I2C Display (nicht unbedingt notwendig, sieht aber gut aus)
2 | Vorkonfektioniertes Relais Boards. Diese können sowohl mit 3,3V aber auf 5V betrieben werden und verfügen bereits über die entsp. Elektronik.
2 | Schraubterminal (3 Pins)
4 | Schraubterminal (2 Pins)
1 | Varistor 250V 250mw
1 | Thermische Sicherung 72°C
1 | Sicherung 250mA (langsam)
1 | Sicherungshalter
1 | 10uF Kondensator
1 | 22uF Kondensator
3 | 100nF Kondensator (Keramik)
3 | 100uF Kondensator
2 | 2,7KOhm Widerstand
1 | 10KOhm Widerstand
1 | Platinennetzteil HLK-PM01 AC DC 220V

Als Gehäuse wurde ein einfacher IP65 Abzweigkasten (Sonderpreisbaumarkt) genutzt. Die Öffnung für das Display wurde mittels einer Laubsäge erstellt und das Display mittels Schmelzkleber befestigt (siehe Bild). Diverse Kleinteile wie Draht, Platine, Steckleisten, etc. finden hier keine gesonderte Erwähnung, da diese Dinge im Fundus vorhanden waren.

Ein befreundeter Elektroniker gab den Hinweis, am Ausgang J2 auch noch einen Varistor mit einzubauen.

Sämtliche Bauteile wurden über den Onlinehandel bezogen.

Seite 6

# ADC Kalibrierung / Temperatursensoren

Je nach verwendeten ESP kann der DAC Probleme bei der Umwandlung der jeweiligen Widerstandswerte machen. Während der Umsetzung wurden bei diversen ESP unterschiedliche Ergebnisse geliefert, was wiederum zu unterschiedlichen Temperaturen führte. Die Berechnung (Glättung) der jeweiligen Werte erfolgt nun mittels einer im Vorfeld generierten Lookup-Tabelle. Für eine passende Erzeugung der Tabellen kann entweder die Lösung von „e-thinkers“ (https://github.com/e-tinkers/esp32-adc-calibrate) oder eine etwas genauere Logik von „Kveri“ (https://github.com/Kveri/esp32-adc-calibrate) verwendet werden. Alternativ können aber auch die mit dem Quellcode-Archiv (Ordner „/sensordata“) bereitgestellten Tabellen „lut34.txt“, „lut36.txt“ und „lut39.txt“ genutzt werden. Die Tabellen beinhalten hierzu die jeweils gemessenen Mittelwerte von 8 unterschiedlichen ESP. Wichtig, bei einer eigenen Messung ist, dass die Anzahl von 4096 (Auflösung DAC) Zeilen einzuhalten sind und die Werte alle als Integer vorliegen müssen.

Bei der Zuordnung der jeweiligen Widerstandswerte von den Temperatursensoren (VR10 / VR11) zum DAC wurden die herstellerspezifischen Tabellen (zu finden auf Seite 26 im
Handbuch | „Für | den | Betreiber/für | den | Fachhandwerker | Bedienungs- | und
Installationsanleitung auroMATIC 560“) herangezogen. Die gemessenen und gemittelten Werte wurden mittels einer Widerstandsdekade nachgebildet und im Abschluss in die Dateien „vrs10.txt“ und „vrs11.txt“ überführt.

Die Berechnung der jeweiligen Temperaturen erfolgt dann im Programm mittels einer Linearen Interpolation (siehe Quellcode tempsensors.ino).

Die generierten Dateien (egal ob selbst oder die aus dem mitgelieferten Archiv) müssen auf die SD-Karte in das Verzeichnis „/sensordata“ kopiert werden. Auf die Namenskonformität ist hierbei zu achten.
Gpio Pin | Name
34 | lut34.txt
36 | lut36.txt
39 | lut39.txt

Seite 7

# Installation

Es besteht die Möglichkeit den Quellcode selbst zu kompilieren oder die bereitgestellten „.bin“ Dateien aus dem Github-Repository (siehe Link github) zu verwenden.

Unabhängig ob Kompilierung oder „.bin“ Nutzung, es muss eine SD-Karte (FAT32) mit folgender Ordnerstruktur vorbereitet werden.
Ordner | Verwendung
/sensordata | Speicherort der Lookup-Dateien
/log | Speicherort für die Logfiles
/webserver | Speicherort der html, js und css Dateien

Im Anschluss sollten die Inhalte aus den gleichnamigen Ordnern des ZIP-Archivs 1:1 in den jeweiligen Ordner überführt werden. Für den Fall das eigenen Lookup-Dateien generiert wurden, sind Diese natürlich zu berücksichtigen.

## Kompilierung

Für die Entwicklung wurde Arduino in der Version 2.3.2 verwendet. Die Dateien (*.ino, *.h)können daher 1:1 in den Ordner eines bestehenden Arduino Projekts kopiert werden. Bitte auf Namensgleichheit („VRS-Replace“) achten.

- Neuen Sketch erstellen
- Sketch unter dem Name „VRS-Replace“ speichern
- Sketch Ordner öffnen
- *.ino & *.h Files in den Ordner aus dem ZIP „/src“ kopieren

Folgende externe Bibliotheken wurden zusätzlich über den „LIBRARY MANAGER“ in das Projekt aufgenommen.

- ArduinoJson
- PsychicHttp
- U8g2lib

Die Kompilierung erfolgt mit dem ausgewählten Board „ESP32-WROOM-DA Module“ und mit dem Partition Scheme „Minimal SPIFFS (1.9MB APP with OTA/190KB SPIFFS)“. Weitere Einstellungen sollten hierfür nicht relevant sein, können aber dem nachfolgenden Screenshot entnommen werden.

Seite 8

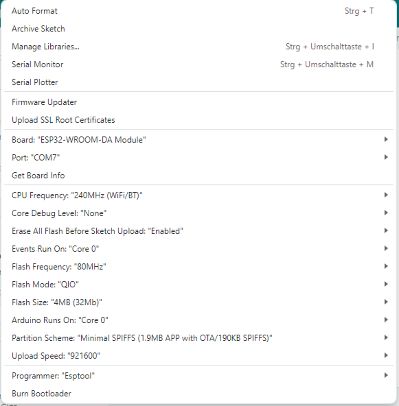
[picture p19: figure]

Ein Wechsel der Entwicklungsumgebung inkl. dem Wechsel auf C++ ist in der Planung.

Seite 9

## *.bin Files

Für die Installation der *.bin Dateien, kann das ESP32 FLASH DOWNLOAD TOOL (hier verwendet Version v3.9.8) verwendet werden. Bitte auf die richtigen Parameter achten.

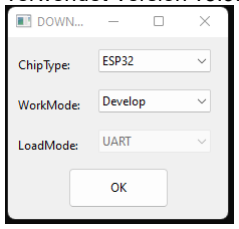
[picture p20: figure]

Die *.bin Dateien müssen entsprechen der folgende Tabelle auch an die jeweiligen Bereiche übertragen werden:
Datei | Address
VRS-Replace.ino.bootloader.bin | 0x1000
VRS-Replace.ino.partitions.bin | 0x8000
VRS-Replace.ino.bin | 0x10000

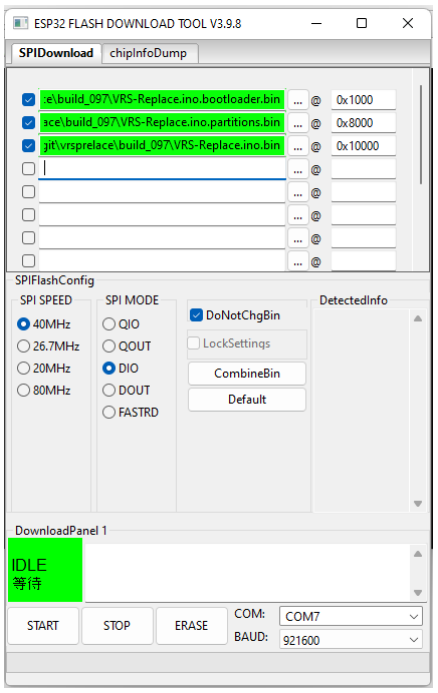
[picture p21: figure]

Seite 10

Der ESP sollte danach neu starten. Für den Fall das keine Konfiguration vorhanden ist, startet das System als AP (siehe Konfiguration / Administration)

Seite 11

# Betrieb

Der mögliche Betrieb kann in folgende Bereiche gegliedert werden.

## Konfiguration / Administration

Ohne irgendwelche Einstellungen, startet das System als Access-Point unter der SSID „VRS-Replace“. Nach Anmeldung mit dem Key „12345678“ kann die Konfigurationsseite durch Eingabe der IP „192.168.4.1“ aufgerufen werden.

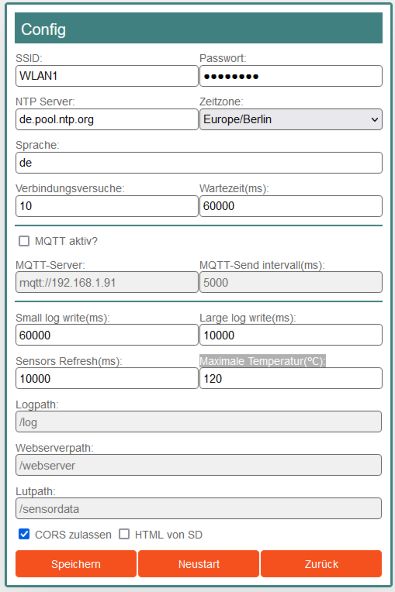
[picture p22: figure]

Parameter | erfordert Neustart | Beschreibung
SSID: | x | SSID des WiFi-Netzwerks
Passwort: | x | Password für die Anmeldung am WiFi-Netzwerk
NTP Server: | | IP oder Domain des NTP-Servers
Zeitzone: | | Auswahl unterschiedlicher europäischer Zeitzonen. Für Deutschland „Europe/Berlin“
Sprache: | | Derzeit werden „de“ = Deutsch und „en“ = Englisch angeboten
Verbindungsversu che: | | Anzahl der Verbindungsversuche bis das Projekt sich wieder als AP meldet.
Wartezeit(ms): | | Wartezeit zwischen den einzelnen Verbindungsversuchen.
MQTT aktiv? | | MQTT aktiv
MQTT-Server: | | URL des MQTT-Servers. Der Term „mqtt://“ muss am Anfange der URL stehen.
MQTT-Send intervall(ms): | | Intervall für den Versand von MQTT-Nachrichten.
Small log write(ms): | | In welchen Zeitabständen soll das „Small“-Log geschrieben werden.

Seite 12

Large log write(ms): | In welchen Zeitabständen soll das „Large“-Log geschrieben werden.
Sensors Refresh(ms): | Aktualisierungszeit der Temperatursensoren
Maximale Temperatur(°C): | Maximal zulässige Temperatur des Kollektorfühler.
Logpath: | Ablageort auf der SD Karte für die Logfiles.
Webserverpath: | Ablageort auf der SD Karte für die HTML/JS/CSS Dateien.
Lutpath: | Ablageort für die LUT-Tabellen. (siehe ADC Kalibrierung / Temperatursensoren)
CORS zulassen? | Soll der HTTP-Server CORS-Anfragen zulassen.
HTML von SD? | Sollen HTML/JS/CSS-Dateien von der SD-Karte geliefert werden.

Nachdem die Konfiguration vorgenommen wurde, kann mittels „Speichern“ und „Neustart“ das System neu gestartet werden. Sollte bei der Konfiguration ein Fehler unterlaufen sein, so startet das System erneut als Access-Point nach (Verbindungsversuche * Wartezeit(ms)).

Mit korrekten Konfigurationswerten startet das System in einer ähnlichen Darstellung.

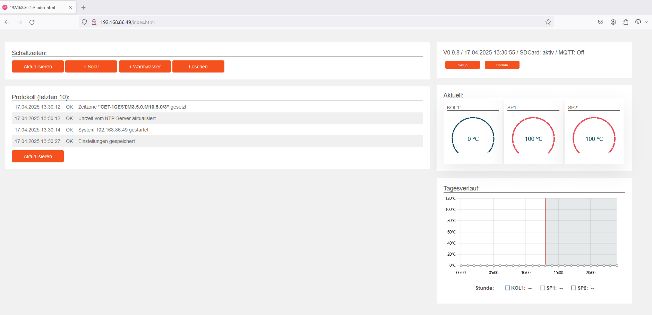
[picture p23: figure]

Obige Darstellung wurde der Entwicklungsumgebung entnommen und hier sind keine Temperaturfühler angeschlossen.

Seite 13

## Timer für Solarpumpe

Ein Druck auf „+ Solar“ öffnet den Dialog für die Erstellung eines neuen Timer für die Solarpumpe.

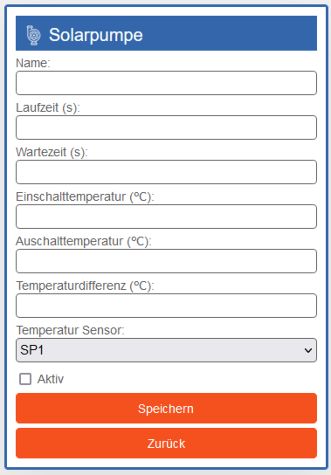
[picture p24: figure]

Parameter: | Beschreibung:
Name: | Name des Timer
Laufzeit (s): | Laufzeit der Pumpe in Sekunden (Timer blinkt rot)
Wartezeit (s): | Wartezeit der Pumpe in Sekunden (Timer blinkt gelb)
Einschalttemperatur (°C): | Ab welcher Temperatur (Kol1) soll die Pumpe aktiviert werden
Ausschalttemperatur (°C): | Zieltemperatur, abhängig von „Temperatur Sensor“
Temperaturdifferenz (°C): | Temperaturdifferenz Kol1 zu „Temperatur Sensor“ zum Starten der Pumpe. Falls die Temperatur kleiner als die Ausschalttemperatur ist und der Timer bereits gestartet wurde, schaltet der Timer in den Wartemodus.
Temperatur Sensor: | Relevanter Temperatursensor Sp1, Sp2 oder Mittelwert
Aktiv | Timer aktiv oder nicht

Seite 14

## Timer für Warmwasser

Ein Druck auf „+ Warmwasser“ öffnet den Dialog für die Erstellung eines neuen Warmwasser-Timer.

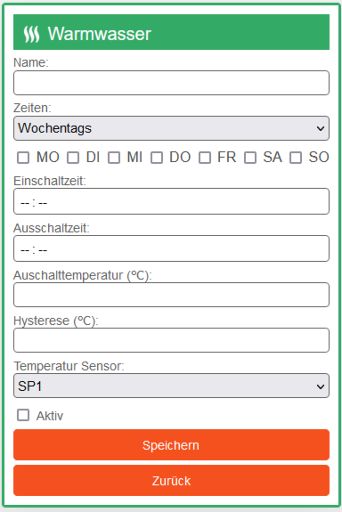
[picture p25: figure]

Parameter | relevantes „Zeiten“ Programm | Beschreibung
Name: | X | Name des Timer
Zeiten: | X | Auswahl der jeweiligen Zeitsteuerung (Täglich/Wochentags/Manuell)
MO, DI, MI, DO, FR, SA, SO | Wochentags | An welchem Wochentag soll der Timer gestartet werden.
Einschaltzeit: | Täglich/Wochentags | Wann soll der Timer gestartet werden HH24:mm
Ausschaltzeit: | Täglich/Wochentags | Wann soll der Timer gestoppt werden HH24:mm
Ausschalttemperatur (°C) | Täglich/Wochentags | Bei welcher Temperatur soll der Timer gestoppt bzw. beendet werden.
Hysterese (°C) | Täglich/Wochentags | Hysterese
Temperatur Sensor: | X | Relevanter Temperatursensor Sp1, Sp2 oder Mittelwert
Aktiv | X | Timer aktiv oder nicht

Seite 15

## Block „Schaltzeiten“

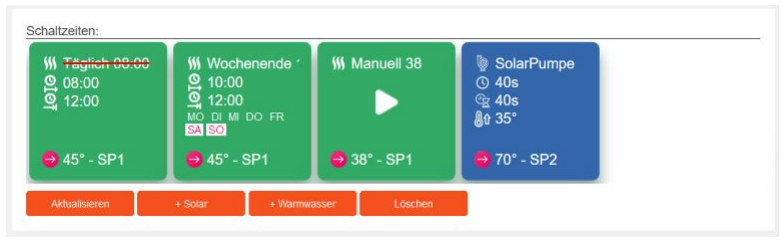
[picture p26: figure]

Der Block „Schaltzeiten“ zeigt sämtliche definierten Programme an. Bei inaktiven Programmen wird der Name mit einem roten Strich durchgestrichen dargestellt. Aktive Timer blinken je nach Status „gelb“ oder „rot“.

Timer vom Typ „Manuell“ könnten durch einen Druck auf das entsp. Symbol „gestartet“ oder „gestoppt“ werden.

Start Timer | Stop Timer

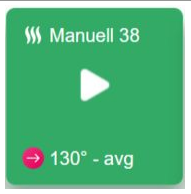
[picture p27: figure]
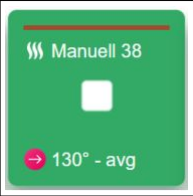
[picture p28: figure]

* In der Chart wurde der Timer auf eine Zieltemperatur von 130°C gesetzt. Das ist natürlich absoluter quatsch und wird auch abgefangen.

Button(s) | Beschreibung
Aktualisieren | Aktualisiert die Timerliste
+ Solar | Öffnet den Dialog für das Hinzufügen eines Solar Timer's
+ Warmwasser | Öffnet den Dialog für das Hinzufügen eines Warmwasser Timer's
Löschen | Markierte Timer werden nach Druck auf diesen Button gelöscht. Es findet keine Warnung statt.

Ein Doppelklick bzw. ein „Longtouch“ auf einen Timer öffnet den Dialog mit den konfigurierten Werten.

Seite 16

## Block „Protokoll (letzten 10)“

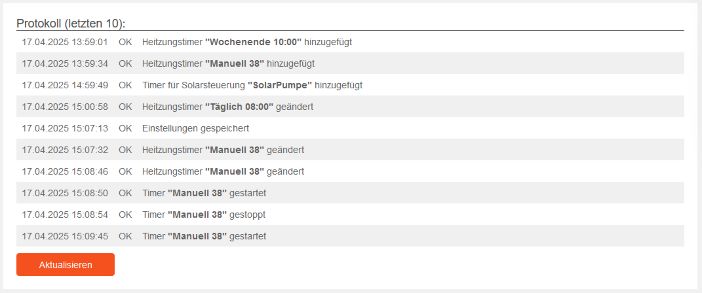
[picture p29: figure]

Zeigt die letzten 10 Protokolleinträge.

Button(s) | Beschreibung
Aktualisieren | Aktualisiert die letzten 10 Einträge

## Block „Status“

Zeigt den aktuellen Systemstatus. Die Version, Datum mit Uhrzeit, ob die SD-Karte aktiv ist und ob die MQTT-Übertragung aktiviert wurde.

Button(s) | Beschreibung
Setup | Öffnet das Konfigurationsmenü
Update | Öffnet den Dialog für das Einspielen einer neuen Version

## Block „Aktuell“

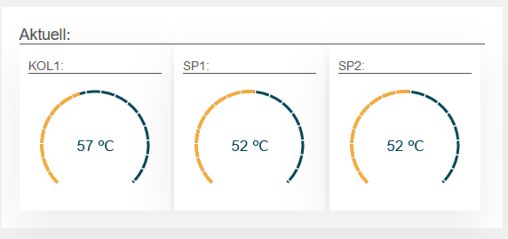
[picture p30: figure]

Zeigt die aktuell gemessene Temperatur des jeweiligen Sensors.

Seite 17

## Block „Tagesverlauf“


Zeigt die aktuelle Temperaturkurve verteilt über den Tag. Der rote Balken markiert die aktuelle Stunde und der graue Bereich zeigt den Temperaturverlauf des gestrigen Tags.

Seite 18

# REST

Die Kommunikation zwischen Front- und Backend erfolgt mittels den aufgelisteten REST Aufrufen. Die verwendetet IP (192.168.80.16) bei einzelnen Beispielen, bezieht sich auf meine Umgebung. Die IP ist daher an die eigene Umgebung anzupassen.

## /status

Bereitstellung aktueller Systeminformationen
Input: | Type: | Beschreibung
NA
Output:
timestamp | string | Zeitstempel im Format
sdmount | bool | Ist die SD-Karte verfügbar(mount)
version | string | Version der Software
sd | bool | Ist das SD-Interface verfügbar
nbtimers | int | Anzahlt der Timer
heap | int | Verfügbarer Heap-Memory (bytes)
mqttactive | bool | Wurde MQTT aktiviert

http://192.168.80.16/status
{"timestamp":"18.04.2025
12:10:26","sdmount":true,"version":"0.9.8","sd":true,"mqttactive":false,"nbtimers":3,"nbtimersactive":0,"heap" :91416}

Seite 19

## /log – Hier Rechtschreibung

Liefert die letzten 10 Protokolleinträge
Input: | Type: | Beschreibung
NA
Output: | Array[10]
id | int | Fortlaufender Nummer
priocode | int | Priorität des Eintrags (Veraltet)
date | int | Datum im Format yyyyMMdd
time | int | Uhrzeit im Format HH24mmss ohne führende Null
code | int | Statuscode (siehe Statuscodes)
message | string | Zusammengesetzte Nachricht. Beispiel: code=201 / message=5!morgens Übersetzt: Timer mit der id=5 und dem Namen=morgens wurde gestoppt

http://192.168.80.16/log

[{"id":5523,"priocode":10,"date":20250418,"time":10629,"code":182,"message":"CET-1CEST,M3.5.0,M10.5.0/3"},
{"id":5524,"priocode":10,"date":20250418,"time":10629,"code":180,"message":""}, {"id":5525,"priocode":10,"date":20250418,"time":10726,"code":125,"message":"192.168.80.16"}, {"id":5526,"priocode":10,"date":20250418,"time":10730,"code":126,"message":"192.168.80.16"}, {"id":5527,"priocode":10,"date":20250418,"time":10730,"code":182,"message":"CET-1CEST,M3.5.0,M10.5.0/3"},
{"id":5528,"priocode":10,"date":20250418,"time":10730,"code":180,"message":""}, {"id":5529,"priocode":10,"date":20250418,"time":32045,"code":125,"message":"192.168.80.16"}, {"id":5530,"priocode":10,"date":20250418,"time":32150,"code":126,"message":"192.168.80.16"}, {"id":5531,"priocode":10,"date":20250418,"time":32150,"code":182,"message":"CET-1CEST,M3.5.0,M10.5.0/3"},
{"id":5532,"priocode":10,"date":20250418,"time":32150,"code":180,"message":""}]

Seite 20

## /downloadtemperaturelog

Ermöglicht den Download von protokollierten Temperaturwerten. Der Aufbau der Dateien existiert in zwei unterschiedlichen Formaten „small“ und „full“. Das Schreiben und somit die Größe des Temperaturlogs „full“ wird durch den Parameter „Large log write(ms):“ (siehe Konfiguration / Administration) beeinflusst.
Input: | Type: | Beschreibung
logfile | int | Datum des gewünschten Logfiles. Format: yyyyMMdd
type | string | „small“ oder „full“
Output: | Startet den Download-Dialog

NA

CSV Dokumentformat small
Spalte: | Type: | Beschreibung
1 | int | Temperatursensor 0=Kol1, 1=Sp1, 2=Sp2
2-25 | double | Maximal gemessene Temperatur zur vollen Stunde
26-49 | double | Minimal gemessene Temperatur zur vollen Stunde

CSV Dokumentformat full
Spalte: | Type: | Beschreibung
1 | int | Datum im Format yyyyMMdd
2 | string | Uhrzeit im Format HH24mmss mit führender Null
3 | int | Id eines aktiven Warmwassertimer (-1 falls kein Programm gestartet)
4 | int | Id eines aktiven Solartimer (-1 falls kein Programm gestartet)
5 | int | Id eines aktiven Zirkulationspumpentimer (Derzeit keine Verwendung, daher immer -1)
6 | string | Name des Temperatursensors (Kol1, Sp1, Sp2)
7 | int | Id des Temperatursensors
8 | double | Aktuell gemessen Temperatur
9 | double | Maximal gemessene Temperatur (pro Tag)
10 | double | Minimal gemessene Temperatur (pro Tag)

Seite 21

## /temperature

Liefert die aktuell gemessenen Temperaturwerte innerhalb eines JSON-Arrays.
Input: | Type: | Beschreibung
NA
Output: | Array[3]
bez | int | Name des Sensors
deviceid | int | Id des Sensors Kol1=0 / Sp1 = 1 / Sp2 = 2
sensortype | int | Sensortyp VR10 = 1 / VR11=2
Ta | double | Aktuelle Temperatur
TaAvg | double | Durchschnittliche Temperatur (Anpassbar im Code sensorAvgTemperatureCalcSize)
TaMin | double | Minimum Temperatur (pro Stunde)
TaMax | double | Maximal Temperatur (pro Stunde)
TaMinH | double Array[24] | Array mit den Minimum Temperaturen pro Stunde
TaMaxH | double Array[24] | Array mit den Maximal Temperaturen pro Stunde
TaMinY | double Array[24] | Array mit den Minimum Temperaturen pro Stunde / Vortag
TaMaxY | double Array[24] | Array mit den Maximal Temperaturen pro Stunde / Vortag

http://192.168.80.16/temperature
[{"bez":"Kol1","deviceid":1,"sensortype":2,"Ta":25.53,"TaAvg":25.59,"TaMin":25.48,"TaMax":26.08,"TaMinH": [8.64,8.48,8.34,8.22,7.97,7.83,7.83,9.58,12.49,16.62,28.76,26.26,31.47,26.01,25.48,55.22,63.67,56.91,21. 28,13.23,10.65,9.58,9.07,8.76],"TaMaxH":[9.11,8.93,8.88,8.81,8.69,8.41,9.72,13.81, … ,"TaMaxHY": [51.27,50.19,49.36,48.51,47.73,47.06,46.38,45.31,44.93,44.14,43.15,40.32,40.06,45.31,50.75,52.09,55.11, 56.87,56.79,55.49,54.18,53.02,52.31,51.87]}]

Seite 22

## /config

Liste mit den vergebenen Konfigurationswerten
Input: | Type: | Beschreibung
NA
Output:
ssid | string | SSID des genutzten Wi-Fi Netzwerks
password | string | Immer ***
ntpserver | string | IP oder Domain des NTP-Servers
lutpath | string | Order auf der SD-Karte für die vorkonfigurierten Sensordaten.
logpath | string | Order auf der SD-Karte für die Ablage der Logfiles
webserverpath | string | Order auf der SD-Karte für die Bereitstellung von html, js, css Dateien.
temperaturesrt | int | Zeit in ms für das messen von Temperaturwerten
temperaturelwt | int | Zeit in ms für das Schreiben von Temperaturwerten (small)
temperatureswt | int | Zeit in ms für das Schreiben von Temperaturwerten (full)
wificonnectionretries | int | Anzahl der Wi-Fi Verbindungsversuche
wifireconnectinterval | int | Zeit zwischen den einzelnen Verbindungsversuchen
maxtemperature | int | Maximale Kollektortemperatur
version | string | Version der installierten Software
allowcors | bool | CORS Zugriffe zulässig?
deliverfromsd | bool | Webdaten werden von der SD-Karte bereitgestellt?
mqttactive | bool | MQTT aktiv?
mqttserver | string | URL des MQTT-Server
mqttsendinterval | int | Intervall (ms) für das Senden von MQTT-Nachrichten
language | string | Sprache (de, en)
timezone | string | Eingestellte Zeitzone

http://192.168.80.16/config

{"ssid":"WLAN1","password":"********","ntpserver":"de.pool.ntp.org","lutpath":"/sensordata","logpath":"/ log","webserverpath":"/
webserver","temperaturesrt":10000,"temperaturelwt":10000,"temperatureswt":60000,"wificonnectionretries": 10,"wifireconnectinterval":60000,"maxtemperature":120,"version":"0.9.8","allowcors":true,"deliverfromsd":fal se,"mqttactive":false,"mqttserver":"mqtt:// 192.168.1.91","mqttsendinterval":5000,"language":"de","timezone":"4;CET-1CEST,M3.5.0,M10.5.0/3"}

Seite 23

## /system

Ermöglicht Systemänderungen durch hinzufügen einer der folgenden Parameter an die URL.
Input: | Type: | Beschreibung
reboot | string | Startet das System neu
ntp | string | Führt einen Abgleich der Uhrzeit über den eingetragenen NTP-Server durch.
eraseconfig | string | Löscht die komplette Konfiguration und startet als AP neu.
Output: | JSON Status
timestamp | int | DatumUhrzeit im Format dd.MM.yyyy HH24:mm:ss
id | int | Id des Timer. Falls der Aufruf sich nicht auf einen Timer bezieht, ist der Wert immer -1.
status | int | 1=Ok / 2=Error
code | int | Statuscode (siehe Statuscodes)

http://192.168.80.16/system?ntp

{"timestamp":"18.04.2025 14:40:07","id":-1,"status":1,"code":112}

Entsprechender Eintrag in dem Block „Protokoll (letzten 10)“

Seite 24

## /changeconfig

Ermöglicht eine Änderung der eingestellten Konfigurationsparameter. Eine Änderung von SSID und/oder vom Password, erfordert einen Neustart.

Input: | Type: | Beschreibung
config | JSON Dokument
JSON Dokument:
ssid | string | SSID des genutzten Wi-Fi Netzwerks
password | string | Immer ***
ntpserver | string | IP oder Domain des NTP-Servers
temperaturesrt | int | Zeit in ms für das messen von Temperaturwerten
temperaturelwt | int | Zeit in ms für das Schreiben von Temperaturwerten (small)
temperatureswt | int | Zeit in ms für das Schreiben von Temperaturwerten (full)
wificonnectionretries | int | Anzahl der Wi-Fi Verbindungsversuche
wifireconnectinterval | int | Zeit zwischen den Verbindungsversuchen
maxtemperature | int | Maximale Kollektortemperatur
Output: | JSON Status
timestamp | int | DatumUhrzeit im Format dd.MM.yyyy HH24:mm:ss
id | int | Id des Timer. Falls der Aufruf sich nicht auf einen Timer bezieht, ist der Wert immer -1.
status | int | 1=Ok / 2=Error
code | int | Statuscode (siehe Statuscodes)

Seite 25

## /timer

Liefert die konfigurierten Werte eines Timer zurück. Wird keine gültige TimerId beim Aufruf als Id übergeben, so wird eine entsp. JSON Status Meldung zurückgeliefert.

Input: | Type: | Timerpro gramm(e) | Relais | Beschreibung
id | int | Alle | Alle | Id des Timer
Output: | JSON Dokume nt
pos | string | Alle | Alle
id | int | Alle | Alle | Eindeutige ID des Timer
bez | string | Alle | Alle | Bezeichnung des Timer
gpiopin | int | Alle | Alle | Verwendeter ESP-Pin
relais | int | Alle | | Zugeordneter Relais-Type: 1=Warmwasser, 2=Solar
time_on | int | 1,2 | 1 | Startzeit Format: H24mmss
time_off | int | 1,2 | 1 | Endzeit Format: H24mmss
weekdays | int Array[7] | 2 | 1 | Wochentage, an denen der Timer gestartet werden soll
running_period | int | | 2 | Wie lange soll der Timer laufen (ms)
waiting_period | int | | 2 | Wie lange soll der Timer warten (ms)
timer_program | int | | 1 | Typ des Timer 1=Täglich, 2=Wochentags, 3=Manuell
temperature_on | int | | 2 | Kol1 Temperatur für das Starten des Timer
temperature_off | int | 1,2,3 | 1,2 | Zieltemperatur
tempsensor | int | Alle | Alle | Relevanter Temperatursensor für das erreichen der Zieltemperatur Keiner=0, Sp1=1, Sp2=2, Avg_Sp1_Sp2=3, Kol1=4
temperature_diff erence | int | | 2 | Temperaturdifferenz Kol1 zu „tempsensor“ für das Starten des Timer
hysteresis | int | 1,2 | 1 | Hysterese
active | bool | Alle | Alle | Timer aktiv?
state | bool | Alle | Alle | Timer gestartet?
timerstatetype | int | Alle | Alle | Derzeitiger Timer-Status 1=On, 2=Off, 3=Wait
runnings | int | Alle | Alle | Anzahl wie oft der Timer bisher gestartet wurde.
waitings | int | Alle | Alle | Anzahl wie oft der Timer bisher gewartet hat.
laststartdate | int | Alle | Alle | Datum des letzten Starts. Format: yyyyMMdd
laststarttime | int | Alle | Alle | Uhrzeit des letzten Starts. Format: H24mmss
publishhomekit | bool | 3 | 1 | Nicht mehr relevant, da keine Unterstützung für Homekit mehr geplant ist. → MQTT
avgtempincreas epermin | int | 1,2,3 | 1,2 | Durchschnittlicher Temperaturanstieg pro Minute (Future)

Seite 26 http://192.168.80.16/timer?id=45 (Ungültig)
{"timestamp":"18.04.2025 15:33:37","id":-1,"status":2,"code":312}

http://192.168.80.16/timer?id=1

{"pos":"0","id":1,"bez":"Manuell 38","gpiopin":16,"relais":1,"time_on":-1,"time_off":-1,"weekdays": [0,0,0,0,0,0,0],"running_period":-1,"waiting_period":-1,"timer_program":3,"temperature_on":-1,"temperature_off":38,"tempsensor":1,"temperature_difference":-1,"hysteresis":-1,"active":true,"state":false,"timerstatetype":2,"runnings":44,"waitings":0,"laststartdate":20250316,"laststartti me":84931,"publishhomekit":false,"avgtempincreasepermin":-1}

Seite 27

## /timerchange

Ermöglicht das Hinzufügen eines neuen oder das Ändern eines existierenden Timer. Hierzu muss folgendes JSON-Dokument gesendet werden.

Input: | Type: | Timerprog ramm(e) | Relais | Beschreibung
timer | JSON Dokument | Alle | Alle

Input JSON Dokument:

id | int | Alle | Alle | Id des Timer oder -1 für einen neuen Timer. Im zurück gegebenen Dokument kann ggf. die neue TimerId entnommen werden.
bez | string | Alle | Alle | Bezeichnung des Timer
gpiopin | int | Alle | Alle | Verwendeter ESP-Pin
relais | int | Alle | | Zugeordneter Relais-Type: 1=Warmwasser, 2=Solar
time_on | int | 1,2 | 1 | Startzeit Format: H24mmss
time_off | int | 1,2 | 1 | Endzeit Format: H24mmss
weekdays | int Array[7] | 2 | 1 | Wochentage, an denen der Timer gestartet werden soll
running_period | int | | 2 | Wie lange soll der Timer laufen (ms)
waiting_period | int | | 2 | Wie lange soll der Timer warten (ms)
timer_program | int | | 1 | Typ des Timer 1=Täglich, 2=Wochentags, 3=Manuell
temperature_on | int | | 2 | Kol1 Temperatur für das Starten des Timer
temperature_off | int | 1,2,3 | 1,2 | Zieltemperatur
tempsensor | int | Alle | Alle | Relevanter Temperatursensor für das erreichen der Zieltemperatur Sp1=1, Sp2=2, Avg_Sp1_Sp2=3
temperature_diff erence | int | | 2 | Temperaturdifferenz Kol1 zu „tempsensor“ für das Starten des Timer
hysteresis | int | 1,2 | 1 | Hysteresse
active | bool | Alle | Alle | Timer aktiv?
Output: | JSON Status | | 1,2 | Durchschnittlicher Temperaturanstieg pro Minute (Future)
timestamp | int | | | DatumUhrzeit im Format dd.MM.yyyy HH24:mm:ss
id | int | . | | Id des Timer. Falls der Aufruf sich nicht auf einen Timer bezieht, ist der Wert immer -1.
status | int | | | 1=Ok / 2=Error
code | int | | | Statuscode (siehe Statuscodes)

Seite 28

## /timerdelete

Der Aufruf löscht einen oder mehrere Timer. Die zu löschenden Timer werden mittels einem Arrays unter der jeweiligen TimerId übergeben. Gestartete Timer werden im Vorfeld beendet.
Input: | Type: | Beschreibung
timers | JSON Array | Array mit den Id’s der zu löschenden Timer.
Output: | JSON Status
timestamp | int | DatumUhrzeit im Format dd.MM.yyyy HH24:mm:ss
id | int | Id des Timer. Falls der Aufruf sich nicht auf einen Timer bezieht, ist der Wert immer -1.
status | int | 1=Ok / 2=Error
code | int | Statuscode (siehe Statuscodes)

http://192.168.80.16/timerdelete?timers={'id':[1,2]}

{"timestamp":"18.04.2025 16:36:34","id":-1,"status":1,"code":311}

## /timerdeleteall

Löscht alle existierenden Timer. Gestartete Timer werden im Vorfeld beendet.
Input: | Type: | Beschreibung
NA
Output: | JSON Status
timestamp | int | DatumUhrzeit im Format dd.MM.yyyy HH24:mm:ss
id | int | Id des Timer. Falls der Aufruf sich nicht auf einen Timer bezieht, ist der Wert immer -1.
status | int | 1=Ok / 2=Error
code | int | Statuscode (siehe Statuscodes)

Seite 29

## /timerlist

Liefert eine Liste als JSON Array mit allen bestehenden Timer.
Input: | Type: | Timerpro gramm(e) | Relais | Beschreibung

NA
Output: | JSON Array
pos | string | Alle | Alle
id | int | Alle | Alle | Eindeutige ID des Timer
bez | string | Alle | Alle | Bezeichnung des Timer
gpiopin | int | Alle | Alle | Verwendeter ESP-Pin
relais | int | Alle | | Zugeordneter Relais-Type: 1=Warmwasser, 2=Solar
time_on | int | 1,2 | 1 | Startzeit Format: H24mmss
time_off | int | 1,2 | 1 | Endzeit Format: H24mmss
weekdays | int Array[7] | 2 | 1 | Wochentage, an denen der Timer gestartet werden soll
running_period | int | | 2 | Wie lange soll der Timer laufen (ms)
waiting_period | int | | 2 | Wie lange soll der Timer warten (ms)
timer_program | int | | 1 | Typ des Timer 1=Täglich, 2=Wochentags, 3=Manuell
temperature_on | int | | 2 | Kol1 Temperatur für das Starten des Timer
temperature_off | int | 1,2,3 | 1,2 | Zieltemperatur
tempsensor | int | Alle | Alle | Relevanter Temperatursensor für das erreichen der Zieltemperatur Keiner=0, Sp1=1, Sp2=2, Avg_Sp1_Sp2=3, Kol1=4
temperature_diff erence | int | | 2 | Temperaturdifferenz Kol1 zu „tempsensor“ für das Starten des Timer
hysteresis | int | 1,2 | 1 | Hysterese
active | bool | Alle | Alle | Timer aktiv?
state | bool | Alle | Alle | Timer gestartet?
timerstatetype | int | Alle | Alle | Derzeitiger Timer-Status 1=On, 2=Off, 3=Wait
runnings | int | Alle | Alle | Anzahl wie oft der Timer bisher gestartet wurde.
waitings | int | Alle | Alle | Anzahl wie oft der Timer bisher gewartet hat.
laststartdate | int | Alle | Alle | Datum des letzten Starts. Format: yyyyMMdd
laststarttime | int | Alle | Alle | Uhrzeit des letzten Starts. Format: H24mmss
publishhomekit | bool | 3 | 1 | Nicht mehr relevant, da keine Unterstützung für Homekit mehr geplant ist. → MQTT
avgtempincreas epermin | int | 1,2,3 | 1,2 | Durchschnittlicher Temperaturanstieg pro Minute (Future)

Seite 30

## /timerstart

Startet einen Timer vom Type „Manuell“ durch Übergabe der entsp. TimerId.
Input: | Type: | Beschreibung
id | int | Id des Timer der gestartet werden soll.
Output: | JSON Status
timestamp | int | DatumUhrzeit im Format dd.MM.yyyy HH24:mm:ss
id | int | Id des Timer. Falls der Aufruf sich nicht auf einen Timer bezieht, ist der Wert immer -1.
status | int | 1=Ok / 2=Error
code | int | Statuscode (siehe Statuscodes)

http://192.168.80.16/timerstart?id=3

{"timestamp":"18.04.2025 16:47:05","id":3,"status":1,"code":305,"message":"3|Manuell 38"}

## /timerstop

Stoppt den Timer durch Übergabe der entsp. TimerId. Nur relevant für Timer vom Type „Manuell“.
Input: | Type: | Beschreibung
id | int | Id des Timer der gestoppt werden soll.
Output: | JSON Status
timestamp | int | DatumUhrzeit im Format dd.MM.yyyy HH24:mm:ss
id | int | Id des Timer. Falls der Aufruf sich nicht auf einen Timer bezieht, ist der Wert immer -1.
status | int | 1=Ok / 2=Error
code | int | Statuscode (siehe Statuscodes)

http://192.168.80.16/timerstop?id=3
{"timestamp":"18.04.2025 16:47:28","id":3,"status":1,"code":307,"message":"3|Manuell 38"}

Seite 31

## /testrelay

Ermöglicht das Testen der angeschlossenen Relais, unabhängig von irgendwelchen Programmen. Timer haben Vorrang und können daher den Status (high, low) überschreiben.
Input: | Type: | Beschreibung
gpio | int | Relevanter GPIO Pin für Low/High Aktivierung. Derzeit GPIO 16 = Warmwasser, GPIO 17 = Solar
onoff | int | On=1 / Off=2
Output: | JSON Status
timestamp | int | DatumUhrzeit im Format dd.MM.yyyy HH24:mm:ss
id | int | Id des Timer. Falls der Aufruf sich nicht auf einen Timer bezieht, ist der Wert immer -1.
status | int | 1=Ok / 2=Error
code | int | Statuscode (siehe Statuscodes)

Seite 32

# MQTT

Das System ist in der Lage mittels MQTT-Messages über einen MQTT-Brokers und anhand von verschiedenen Topics zu kommunizieren.


Readable Topics
Topic: | Type: | Beschreibung:
/vrsreplace | string | Generelle Statusinformationen. Diese Topic beinhaltet auch den LWT (online/offline).
/vrsreplace/status | json | Statusinformationen analog wie beim REST-Server „/status“
/vrsreplace/sensor/[Sensor] | double | Aktuelle gemessene Temperatur für den jeweiligen Sensor „[Kol1, Sp1, Sp2]“
/vrsreplace/timer/[Timer ID] | json | Status der verfügbaren Timer
/vrsreplace/message | string | Zuletzt publizierter Logeintrag

Writeable Topic
Topic: | Type: | Beschreibung:
/vrsreplace/timer/[Timer ID]/cmd | string | Alle Timer können aktiviert oder deaktiviert werden. Hierzu wird unter der jeweiligen „Timer ID“ der Befehl „activate“ oder „deactivate“ gesendet. Manuelle Timer (Type 3) können zusätzlich gestartet „cmd=start“ oder gestoppt „cmd=stop“ werden.

Seite 33

# Prometheus metrics

Einzelne Werte können auch über Prometheus https://prometheus.io protokolliert und im Anschluss mittels Grafana https://grafana.com/ analysiert werden.


Die Einbindung in Prometheus erfolgt durch einen Eintrag in der Datei „prometheus.yml“ innerhalb der Sektion „scrape_configs“. Bitte unbedingt auf das notwendige Format (Anzahl Blanks) achten!

- job_name: 'vrsreplace'
scrape_interval: 10s # >= Depending on your meassurement interval static_configs:
- targets: ['<IP of VRS-Replace>']
metrics_path: /metrics

Folgende Metriken werden geliefert
Metrik | Beschreibung
vrsreplace_info | {name="vrsreplace",arch="ESP32-D0WD",mac="84:0D:8E:E9:80:E0",version="0.9.8"} 1
vrsreplace_uptime | Zeit in Sekunden seit Start
vrsreplace_heap_size | Größe des Heap
vrsreplace_free_heap_size | Größe des freien Heap
vrsreplace_biggest_heap_block | Größe des größten freien Heap Blocks
vrsreplace_heap_min_free | Minimale Heap Größe seit Start
vrsreplace_wifi_rssi | Wert RSSI
vrsreplace_wifi_station | BSSID des Routers
vrsreplace_temperature | Aktuell gemessene Temperatur für alle Sensoren
vrsreplace_timer | Alle derzeit existierenden Timer mit aktuellem Status. id=TimerId, bez=Bezeichnung, relaistype=Solar/2 oder Warmwasser/1, timerprogram=Vergebenes Timerprogramm, tempsensor=Zugeordneter Temperatursensor

Seite 34

# Statuscodes

Code | Status | Beschreibung
100 | OK | System gestartet
101 | OK | Tageswechsel
110 | Error | Unbekannter Systemaufruf
111 | OK | System wird neu gestartet
112 | OK | NTP Uhrzeit aktualisiert
113 | OK | Firmware aktualisiert
114 | ERROR | Firmware konnte nicht aktualisiert werden
115 | OK | ADC-Wandler erfolgreich deaktiviert
116 | ERROR | ADC-Wandler konnten nicht deaktiviert werden
117 | OK | Einstellungen gespeichert
118 | OK | Einstellungen wurden erfolgreich gespeichert. Neustart erforderlich.
119 | OK | System wurde erfolgreich zurückgesetzt
120 | ERROR | Einstellungen konnten nicht gespeichert werden
121 | ERROR | Lut file konnte nicht gefunden werden
122 | ERROR | Keine SD Karte vorhanden und/oder nicht beschreibbar
125 | ERROR | Wi-Fi Verbindung unterbrochen
126 | OK | Wi-Fi Verbindung wieder hergestellt
127 | OK | System wurde im Config-Modus gestartet
180 | OK | Uhrzeit vom NTP-Server aktualisiert
181 | ERROR | Uhrzeit konnte nicht gesetzt werden
182 | OK | Zeitzone gesetzt
200 | OK | Timer gestartet
201 | OK | Timer gestoppt
202 | OK | Timer wurde in den Wait-State versetzt
203 | OK | Timer wurde restartet
204 | OK | Alle Timer wurden gelöscht
205 | ERROR | Timer konnten nicht gelöscht werden
206 | OK | Timer wurde gelöscht
207 | OK | Timer für Warmwasser hinzugefügt
208 | OK | Timer für Solarsteuerung hinzugefügt
209 | OK | Timer für Zirkulationspumpe hinzugefügt
210 | OK | Timer für Warmwasser geändert
211 | OK | Parameter für Solarsteuerung geändert
212 | OK | Schaltzeiten für Zirkulationssysteme geändert
300 | ERROR | Timer konnte nicht gestartet werden, da kein ID Parameter im Aufruf vorhanden

Seite 35

301 | ERROR | Timer konnte nicht gestartet werden, da ID nicht vorhanden
302 | ERROR | Timer mit der übergebenen ID, wurde bereits gestartet
303 | ERROR | Ein Timer mit dem gewählten Relais-Type, wurde bereits gestartet
304 | OK | Timer wurde deaktiviert
305 | OK | Timer gestartet
306 | ERROR | Timer konnte nicht gestoppt werden, kein ID Parameter im Aufruf vorhanden
307 | OK | Timer gestoppt
308 | ERROR | Timer konnte nicht gestoppt werden, da kein laufender Timer mit der ID gefunden wurde
309 | ERROR | Timer(s) konnten nicht gelöscht werden, keine ID's übergeben
310 | ERROR | Genereller Fehler beim Löschen der Timer
311 | OK | Timer(s) erfolgreich gelöscht
312 | ERROR | Timer nicht gefunden. ID nicht vorhanden
313 | ERROR | Timer nicht gefunden. Keine ID beim Aufruf übergeben
314 | ERROR | Timer konnte nicht geändert werden. Es wurde kein Timer übergeben
315 | ERROR | Genereller Fehler beim Ändern des Timer
316 | OK | Timer hinzugefügt
317 | OK | Timer geändert
340 | OK | Webservice Connect
341 | OK | Erfolgreiche Abmeldung von Client
350 | OK | Firmwareupdate gestartet
351 | ERROR | Fehler beim Firmwareupdate
352 | OK | Firmwareupdate erfolgreich ausgeführt.
353 | ERROR | Parameter konnten nicht geladen werden.
360 | ERROR | Config konnte nicht geändert werden
361 | ERROR | Conifg nicht vorhanden
370 | OK | MQTT gestartet
371 | OK | MQTT gestoppt
372 | ERROR | MQTT Fehler
373 | OK | MQTT wurde initialisiert
374 | ERROR | MQTT konnte nicht initialisiert werden

Seite 36

# Zusätzlich verwendete Softwarekomponenten

Das System verwendet folgende zusätzliche OpenSoruce Komponenten.

- HTMX
https://htmx.org/ https://github.com/bigskysoftware/htmx
- svg-gauge
https://github.com/naikus/svg-gauge
- uPlot
https://github.com/leeoniya/uPlot
- PsychicHttp
https://github.com/hoeken/PsychicHttp

# Zukunft

Folgende „Futures“ sind geplant.

- Umstellung Entwicklungsumgebung
- Umstellung auf C++
- Neues FE ggf. auf Basis von „vue.js“
- Ethernet
- SSL
- Auth User/Password
- Dynamische Programme („Solar“/ „Legionellen“)
- mDNS
- Ertragskalkulation
- ggf. Verzicht auf SD-Card und nur noch Logging über externe Systeme.
- Unterstützung weiterer Temperaturfühler über Regelung mittels AD5270.
- Bessere Fehlererkennung und Benachrichtigung u.A. von „vergammelten Sensoren“.

Seite 37

# Lizenz

GNU GENERAL PUBLIC LICENSE
Version 3, 29 June 2007

Copyright (C) 2007 Free Software Foundation, Inc. <https://fsf.org/> Everyone is permitted to copy and distribute verbatim copies
of this license document, but changing it is not allowed.

Preamble

The GNU General Public License is a free, copyleft license for software and other kinds of works.

The licenses for most software and other practical works are designed to take away your freedom to share and change the works. By contrast, the GNU General Public License is intended to guarantee your freedom to share and change all versions of a program--to make sure it remains free software for all its users. We, the Free Software Foundation, use the GNU General Public License for most of our software; it applies also to any other work released this way by its authors. You can apply it to your programs, too.

When we speak of free software, we are referring to freedom, not price. Our General Public Licenses are designed to make sure that you have the freedom to distribute copies of free software (and charge for them if you wish), that you receive source code or can get it if you want it, that you can change the software or use pieces of it in new free programs, and that you know you can do these things.

To protect your rights, we need to prevent others from denying you these rights or asking you to surrender the rights. Therefore, you have certain responsibilities if you distribute copies of the software, or if you modify it: responsibilities to respect the freedom of others.

For example, if you distribute copies of such a program, whether gratis or for a fee, you must pass on to the recipients the same freedoms that you received. You must make sure that they, too, receive or can get the source code. And you must show them these terms so they know their rights.

Developers that use the GNU GPL protect your rights with two steps:
(1) assert copyright on the software, and (2) offer you this License giving you legal permission to copy, distribute and/or modify it.

For the developers' and authors' protection, the GPL clearly explains that there is no warranty for this free software. For both users' and authors' sake, the GPL requires that modified versions be marked as changed, so that their problems will not be attributed erroneously to authors of previous versions.

Some devices are designed to deny users access to install or run modified versions of the software inside them, although the manufacturer can do so. This is fundamentally incompatible with the aim of protecting users' freedom to change the software. The systematic pattern of such abuse occurs in the area of products for individuals to use, which is precisely where it is most unacceptable. Therefore, we have designed this version of the GPL to prohibit the practice for those

Seite 38 products. If such problems arise substantially in other domains, we stand ready to extend this provision to those domains in future versions of the GPL, as needed to protect the freedom of users.

Finally, every program is threatened constantly by software patents. States should not allow patents to restrict development and use of software on general-purpose computers, but in those that do, we wish to avoid the special danger that patents applied to a free program could make it effectively proprietary. To prevent this, the GPL assures that patents cannot be used to render the program non-free.

The precise terms and conditions for copying, distribution and modification follow.

TERMS AND CONDITIONS

0. Definitions.

"This License" refers to version 3 of the GNU General Public License.

"Copyright" also means copyright-like laws that apply to other kinds of works, such as semiconductor masks.

"The Program" refers to any copyrightable work licensed under this License. Each licensee is addressed as "you". "Licensees" and "recipients" may be individuals or organizations.

To "modify" a work means to copy from or adapt all or part of the work in a fashion requiring copyright permission, other than the making of an exact copy. The resulting work is called a "modified version" of the earlier work or a work "based on" the earlier work.

A "covered work" means either the unmodified Program or a work based on the Program.

To "propagate" a work means to do anything with it that, without permission, would make you directly or secondarily liable for infringement under applicable copyright law, except executing it on a computer or modifying a private copy. Propagation includes copying, distribution (with or without modification), making available to the public, and in some countries other activities as well.

To "convey" a work means any kind of propagation that enables other parties to make or receive copies. Mere interaction with a user through a computer network, with no transfer of a copy, is not conveying.

An interactive user interface displays "Appropriate Legal Notices"
to the extent that it includes a convenient and prominently visible feature that (1) displays an appropriate copyright notice, and (2) tells the user that there is no warranty for the work (except to the extent that warranties are provided), that licensees may convey the work under this License, and how to view a copy of this License. If the interface presents a list of user commands or options, such as a menu, a prominent item in the list meets this criterion.
1. Source Code.

The "source code" for a work means the preferred form of the work for making modifications to it. "Object code" means any non-source form of a work.

Seite 39

A "Standard Interface" means an interface that either is an official standard defined by a recognized standards body, or, in the case of interfaces specified for a particular programming language, one that is widely used among developers working in that language.

The "System Libraries" of an executable work include anything, other than the work as a whole, that (a) is included in the normal form of packaging a Major Component, but which is not part of that Major Component, and (b) serves only to enable use of the work with that Major Component, or to implement a Standard Interface for which an implementation is available to the public in source code form. A "Major Component", in this context, means a major essential component (kernel, window system, and so on) of the specific operating system (if any) on which the executable work runs, or a compiler used to produce the work, or an object code interpreter used to run it.

The "Corresponding Source" for a work in object code form means all the source code needed to generate, install, and (for an executable work) run the object code and to modify the work, including scripts to control those activities. However, it does not include the work's System Libraries, or general-purpose tools or generally available free programs which are used unmodified in performing those activities but which are not part of the work. For example, Corresponding Source includes interface definition files associated with source files for the work, and the source code for shared libraries and dynamically linked subprograms that the work is specifically designed to require, such as by intimate data communication or control flow between those subprograms and other parts of the work.

The Corresponding Source need not include anything that users
can regenerate automatically from other parts of the Corresponding Source.

The Corresponding Source for a work in source code form is that same work.

2. Basic Permissions.

All rights granted under this License are granted for the term of copyright on the Program, and are irrevocable provided the stated conditions are met. This License explicitly affirms your unlimited permission to run the unmodified Program. The output from running a covered work is covered by this License only if the output, given its content, constitutes a covered work. This License acknowledges your rights of fair use or other equivalent, as provided by copyright law.

You may make, run and propagate covered works that you do not convey, without conditions so long as your license otherwise remains in force. You may convey covered works to others for the sole purpose of having them make modifications exclusively for you, or provide you with facilities for running those works, provided that you comply with the terms of this License in conveying all material for which you do not control copyright. Those thus making or running the covered works for you must do so exclusively on your behalf, under your direction and control, on terms that prohibit them from making any copies of your copyrighted material outside their relationship with you.

Conveying under any other circumstances is permitted solely under the conditions stated below. Sublicensing is not allowed; section 10

Seite 40

makes it unnecessary.

3. Protecting Users' Legal Rights From Anti-Circumvention Law.

No covered work shall be deemed part of an effective technological measure under any applicable law fulfilling obligations under article 11 of the WIPO copyright treaty adopted on 20 December 1996, or similar laws prohibiting or restricting circumvention of such
measures.

When you convey a covered work, you waive any legal power to forbid circumvention of technological measures to the extent such circumvention is effected by exercising rights under this License with respect to
the covered work, and you disclaim any intention to limit operation or modification of the work as a means of enforcing, against the work's users, your or third parties' legal rights to forbid circumvention of technological measures.
4. Conveying Verbatim Copies.

You may convey verbatim copies of the Program's source code as you receive it, in any medium, provided that you conspicuously and appropriately publish on each copy an appropriate copyright notice; keep intact all notices stating that this License and any non-permissive terms added in accord with section 7 apply to the code; keep intact all notices of the absence of any warranty; and give all recipients a copy of this License along with the Program.

You may charge any price or no price for each copy that you convey, and you may offer support or warranty protection for a fee.

5. Conveying Modified Source Versions.

You may convey a work based on the Program, or the modifications to produce it from the Program, in the form of source code under the
terms of section 4, provided that you also meet all of these conditions:
a) The work must carry prominent notices stating that you modified it, and giving a relevant date.
b) The work must carry prominent notices stating that it is released under this License and any conditions added under section
7. This requirement modifies the requirement in section 4 to "keep intact all notices".
c) You must license the entire work, as a whole, under this License to anyone who comes into possession of a copy. This License will therefore apply, along with any applicable section 7 additional terms, to the whole of the work, and all its parts, regardless of how they are packaged. This License gives no permission to license the work in any other way, but it does not invalidate such permission if you have separately received it.
d) If the work has interactive user interfaces, each must display Appropriate Legal Notices; however, if the Program has interactive interfaces that do not display Appropriate Legal Notices, your work need not make them do so.

A compilation of a covered work with other separate and independent works, which are not by their nature extensions of the covered work,

Seite 41 and which are not combined with it such as to form a larger program, in or on a volume of a storage or distribution medium, is called an "aggregate" if the compilation and its resulting copyright are not used to limit the access or legal rights of the compilation's users beyond what the individual works permit. Inclusion of a covered work in an aggregate does not cause this License to apply to the other parts of the aggregate.

6. Conveying Non-Source Forms.

You may convey a covered work in object code form under the terms of sections 4 and 5, provided that you also convey the machine-readable Corresponding Source under the terms of this License, in one of these ways:

a) Convey the object code in, or embodied in, a physical product (including a physical distribution medium), accompanied by the Corresponding Source fixed on a durable physical medium customarily used for software interchange.
b) Convey the object code in, or embodied in, a physical product (including a physical distribution medium), accompanied by a written offer, valid for at least three years and valid for as long as you offer spare parts or customer support for that product model, to give anyone who possesses the object code either (1) a copy of the Corresponding Source for all the software in the product that is covered by this License, on a durable physical medium customarily used for software interchange, for a price no more than your reasonable cost of physically performing this conveying of source, or (2) access to copy the
Corresponding Source from a network server at no charge.
c) Convey individual copies of the object code with a copy of the written offer to provide the Corresponding Source. This alternative is allowed only occasionally and noncommercially, and only if you received the object code with such an offer, in accord with subsection 6b.
d) Convey the object code by offering access from a designated place (gratis or for a charge), and offer equivalent access to the Corresponding Source in the same way through the same place at no further charge. You need not require recipients to copy the Corresponding Source along with the object code. If the place to copy the object code is a network server, the Corresponding Source may be on a different server (operated by you or a third party) that supports equivalent copying facilities, provided you maintain clear directions next to the object code saying where to find the Corresponding Source. Regardless of what server hosts the Corresponding Source, you remain obligated to ensure that it is available for as long as needed to satisfy these requirements.
e) Convey the object code using peer-to-peer transmission, provided you inform other peers where the object code and Corresponding Source of the work are being offered to the general public at no charge under subsection 6d.

A separable portion of the object code, whose source code is excluded from the Corresponding Source as a System Library, need not be included in conveying the object code work.

Seite 42

A "User Product" is either (1) a "consumer product", which means any tangible personal property which is normally used for personal, family, or household purposes, or (2) anything designed or sold for incorporation into a dwelling. In determining whether a product is a consumer product, doubtful cases shall be resolved in favor of coverage. For a particular product received by a particular user, "normally used" refers to a typical or common use of that class of product, regardless of the status of the particular user or of the way in which the particular user actually uses, or expects or is expected to use, the product. A product is a consumer product regardless of whether the product has substantial commercial, industrial or non-consumer uses, unless such uses represent the only significant mode of use of the product.

"Installation Information" for a User Product means any methods, procedures, authorization keys, or other information required to install and execute modified versions of a covered work in that User Product from a modified version of its Corresponding Source. The information must suffice to ensure that the continued functioning of the modified object code is in no case prevented or interfered with solely because modification has been made.

If you convey an object code work under this section in, or with, or specifically for use in, a User Product, and the conveying occurs as part of a transaction in which the right of possession and use of the User Product is transferred to the recipient in perpetuity or for a fixed term (regardless of how the transaction is characterized), the Corresponding Source conveyed under this section must be accompanied by the Installation Information. But this requirement does not apply if neither you nor any third party retains the ability to install modified object code on the User Product (for example, the work has been installed in ROM).

The requirement to provide Installation Information does not include a requirement to continue to provide support service, warranty, or updates for a work that has been modified or installed by the recipient, or for the User Product in which it has been modified or installed. Access to a network may be denied when the modification itself materially and adversely affects the operation of the network or violates the rules and protocols for communication across the network.

Corresponding Source conveyed, and Installation Information provided, in accord with this section must be in a format that is publicly documented (and with an implementation available to the public in source code form), and must require no special password or key for unpacking, reading or copying.

7. Additional Terms.

"Additional permissions" are terms that supplement the terms of this License by making exceptions from one or more of its conditions. Additional permissions that are applicable to the entire Program shall be treated as though they were included in this License, to the extent that they are valid under applicable law. If additional permissions apply only to part of the Program, that part may be used separately under those permissions, but the entire Program remains governed by this License without regard to the additional permissions.

When you convey a copy of a covered work, you may at your option remove any additional permissions from that copy, or from any part of it. (Additional permissions may be written to require their own

Seite 43 removal in certain cases when you modify the work.) You may place additional permissions on material, added by you to a covered work,
for which you have or can give appropriate copyright permission.

Notwithstanding any other provision of this License, for material you add to a covered work, you may (if authorized by the copyright holders of that material) supplement the terms of this License with terms:

a) Disclaiming warranty or limiting liability differently from the terms of sections 15 and 16 of this License; or
b) Requiring preservation of specified reasonable legal notices or author attributions in that material or in the Appropriate Legal Notices displayed by works containing it; or
c) Prohibiting misrepresentation of the origin of that material, or requiring that modified versions of such material be marked in reasonable ways as different from the original version; or
d) Limiting the use for publicity purposes of names of licensors or authors of the material; or
e) Declining to grant rights under trademark law for use of some trade names, trademarks, or service marks; or
f) Requiring indemnification of licensors and authors of that material by anyone who conveys the material (or modified versions of it) with contractual assumptions of liability to the recipient, for any liability that these contractual assumptions directly impose on those licensors and authors.

All other non-permissive additional terms are considered "further restrictions" within the meaning of section 10. If the Program as you received it, or any part of it, contains a notice stating that it is governed by this License along with a term that is a further restriction, you may remove that term. If a license document contains a further restriction but permits relicensing or conveying under this License, you may add to a covered work material governed by the terms of that license document, provided that the further restriction does not survive such relicensing or conveying.

If you add terms to a covered work in accord with this section, you must place, in the relevant source files, a statement of the additional terms that apply to those files, or a notice indicating where to find the applicable terms.

Additional terms, permissive or non-permissive, may be stated in the form of a separately written license, or stated as exceptions;
the above requirements apply either way.
8. Termination.

You may not propagate or modify a covered work except as expressly provided under this License. Any attempt otherwise to propagate or modify it is void, and will automatically terminate your rights under this License (including any patent licenses granted under the third paragraph of section 11).

However, if you cease all violation of this License, then your license from a particular copyright holder is reinstated (a)

Seite 44 provisionally, unless and until the copyright holder explicitly and finally terminates your license, and (b) permanently, if the copyright holder fails to notify you of the violation by some reasonable means prior to 60 days after the cessation.

Moreover, your license from a particular copyright holder is reinstated permanently if the copyright holder notifies you of the violation by some reasonable means, this is the first time you have received notice of violation of this License (for any work) from that copyright holder, and you cure the violation prior to 30 days after your receipt of the notice.

Termination of your rights under this section does not terminate the licenses of parties who have received copies or rights from you under this License. If your rights have been terminated and not permanently reinstated, you do not qualify to receive new licenses for the same material under section 10.

9. Acceptance Not Required for Having Copies.

You are not required to accept this License in order to receive or run a copy of the Program. Ancillary propagation of a covered work occurring solely as a consequence of using peer-to-peer transmission to receive a copy likewise does not require acceptance. However, nothing other than this License grants you permission to propagate or modify any covered work. These actions infringe copyright if you do not accept this License. Therefore, by modifying or propagating a covered work, you indicate your acceptance of this License to do so.

10. Automatic Licensing of Downstream Recipients.

Each time you convey a covered work, the recipient automatically receives a license from the original licensors, to run, modify and propagate that work, subject to this License. You are not responsible for enforcing compliance by third parties with this License.

An "entity transaction" is a transaction transferring control of an organization, or substantially all assets of one, or subdividing an organization, or merging organizations. If propagation of a covered work results from an entity transaction, each party to that transaction who receives a copy of the work also receives whatever licenses to the work the party's predecessor in interest had or could give under the previous paragraph, plus a right to possession of the Corresponding Source of the work from the predecessor in interest, if the predecessor has it or can get it with reasonable efforts.

You may not impose any further restrictions on the exercise of the rights granted or affirmed under this License. For example, you may not impose a license fee, royalty, or other charge for exercise of rights granted under this License, and you may not initiate litigation (including a cross-claim or counterclaim in a lawsuit) alleging that any patent claim is infringed by making, using, selling, offering for sale, or importing the Program or any portion of it.

11. Patents.

A "contributor" is a copyright holder who authorizes use under this License of the Program or a work on which the Program is based. The work thus licensed is called the contributor's "contributor version".

Seite 45

A contributor's "essential patent claims" are all patent claims owned or controlled by the contributor, whether already acquired or hereafter acquired, that would be infringed by some manner, permitted by this License, of making, using, or selling its contributor version, but do not include claims that would be infringed only as a consequence of further modification of the contributor version. For purposes of this definition, "control" includes the right to grant patent sublicenses in a manner consistent with the requirements of this License.

Each contributor grants you a non-exclusive, worldwide, royalty-free patent license under the contributor's essential patent claims, to make, use, sell, offer for sale, import and otherwise run, modify and propagate the contents of its contributor version.

In the following three paragraphs, a "patent license" is any express agreement or commitment, however denominated, not to enforce a patent (such as an express permission to practice a patent or covenant not to sue for patent infringement). To "grant" such a patent license to a party means to make such an agreement or commitment not to enforce a patent against the party.

If you convey a covered work, knowingly relying on a patent license, and the Corresponding Source of the work is not available for anyone to copy, free of charge and under the terms of this License, through a publicly available network server or other readily accessible means, then you must either (1) cause the Corresponding Source to be so available, or (2) arrange to deprive yourself of the benefit of the patent license for this particular work, or (3) arrange, in a manner consistent with the requirements of this License, to extend the patent license to downstream recipients. "Knowingly relying" means you have actual knowledge that, but for the patent license, your conveying the covered work in a country, or your recipient's use of the covered work in a country, would infringe one or more identifiable patents in that country that you have reason to believe are valid.

If, pursuant to or in connection with a single transaction or arrangement, you convey, or propagate by procuring conveyance of, a covered work, and grant a patent license to some of the parties receiving the covered work authorizing them to use, propagate, modify or convey a specific copy of the covered work, then the patent license you grant is automatically extended to all recipients of the covered work and works based on it.

A patent license is "discriminatory" if it does not include within the scope of its coverage, prohibits the exercise of, or is conditioned on the non-exercise of one or more of the rights that are specifically granted under this License. You may not convey a covered work if you are a party to an arrangement with a third party that is in the business of distributing software, under which you make payment to the third party based on the extent of your activity of conveying the work, and under which the third party grants, to any of the parties who would receive the covered work from you, a discriminatory patent license (a) in connection with copies of the covered work conveyed by you (or copies made from those copies), or (b) primarily for and in connection with specific products or compilations that contain the covered work, unless you entered into that arrangement, or that patent license was granted, prior to 28 March 2007.

Nothing in this License shall be construed as excluding or limiting

Seite 46 any implied license or other defenses to infringement that may otherwise be available to you under applicable patent law.

12. No Surrender of Others' Freedom.

If conditions are imposed on you (whether by court order, agreement or otherwise) that contradict the conditions of this License, they do not excuse you from the conditions of this License. If you cannot convey a covered work so as to satisfy simultaneously your obligations under this License and any other pertinent obligations, then as a consequence you may not convey it at all. For example, if you agree to terms that obligate you to collect a royalty for further conveying from those to whom you convey the Program, the only way you could satisfy both those terms and this License would be to refrain entirely from conveying the Program.

13. Use with the GNU Affero General Public License.

Notwithstanding any other provision of this License, you have permission to link or combine any covered work with a work licensed under version 3 of the GNU Affero General Public License into a single combined work, and to convey the resulting work. The terms of this License will continue to apply to the part which is the covered work, but the special requirements of the GNU Affero General Public License, section 13, concerning interaction through a network will apply to the combination as such.

14. Revised Versions of this License.

The Free Software Foundation may publish revised and/or new versions of the GNU General Public License from time to time. Such new versions will be similar in spirit to the present version, but may differ in detail to address new problems or concerns.

Each version is given a distinguishing version number. If the Program specifies that a certain numbered version of the GNU General Public License "or any later version" applies to it, you have the option of following the terms and conditions either of that numbered version or of any later version published by the Free Software Foundation. If the Program does not specify a version number of the GNU General Public License, you may choose any version ever published by the Free Software Foundation.

If the Program specifies that a proxy can decide which future versions of the GNU General Public License can be used, that proxy's public statement of acceptance of a version permanently authorizes you to choose that version for the Program.

Later license versions may give you additional or different permissions. However, no additional obligations are imposed on any author or copyright holder as a result of your choosing to follow a later version.

15. Disclaimer of Warranty.

THERE IS NO WARRANTY FOR THE PROGRAM, TO THE EXTENT PERMITTED BY APPLICABLE LAW. EXCEPT WHEN OTHERWISE STATED IN WRITING THE COPYRIGHT HOLDERS AND/OR OTHER PARTIES PROVIDE THE PROGRAM "AS IS" WITHOUT WARRANTY OF ANY KIND, EITHER EXPRESSED OR IMPLIED, INCLUDING, BUT NOT LIMITED TO, THE IMPLIED WARRANTIES OF MERCHANTABILITY AND FITNESS FOR A PARTICULAR PURPOSE. THE ENTIRE RISK AS TO THE QUALITY AND PERFORMANCE OF THE PROGRAM

Seite 47

IS WITH YOU. SHOULD THE PROGRAM PROVE DEFECTIVE, YOU ASSUME THE COST OF ALL NECESSARY SERVICING, REPAIR OR CORRECTION.

16. Limitation of Liability.

IN NO EVENT UNLESS REQUIRED BY APPLICABLE LAW OR AGREED TO IN WRITING WILL ANY COPYRIGHT HOLDER, OR ANY OTHER PARTY WHO MODIFIES AND/OR CONVEYS THE PROGRAM AS PERMITTED ABOVE, BE LIABLE TO YOU FOR DAMAGES, INCLUDING ANY GENERAL, SPECIAL, INCIDENTAL OR CONSEQUENTIAL DAMAGES ARISING OUT OF THE USE OR INABILITY TO USE THE PROGRAM (INCLUDING BUT NOT LIMITED TO LOSS OF DATA OR DATA BEING RENDERED INACCURATE OR LOSSES SUSTAINED BY YOU OR THIRD PARTIES OR A FAILURE OF THE PROGRAM TO OPERATE WITH ANY OTHER PROGRAMS), EVEN IF SUCH HOLDER OR OTHER PARTY HAS BEEN ADVISED OF THE POSSIBILITY OF SUCH DAMAGES.

17. Interpretation of Sections 15 and 16.

If the disclaimer of warranty and limitation of liability provided above cannot be given local legal effect according to their terms, reviewing courts shall apply local law that most closely approximates an absolute waiver of all civil liability in connection with the Program, unless a warranty or assumption of liability accompanies a copy of the Program in return for a fee.

END OF TERMS AND CONDITIONS

How to Apply These Terms to Your New Programs

If you develop a new program, and you want it to be of the greatest possible use to the public, the best way to achieve this is to make it free software which everyone can redistribute and change under these terms.

To do so, attach the following notices to the program. It is safest
to attach them to the start of each source file to most effectively
state the exclusion of warranty; and each file should have at least
the "copyright" line and a pointer to where the full notice is found.

<one line to give the program's name and a brief idea of what it does.> Copyright (C) <year> <name of author>

This program is free software: you can redistribute it and/or modify it under the terms of the GNU General Public License as published by the Free Software Foundation, either version 3 of the License, or (at your option) any later version.

This program is distributed in the hope that it will be useful,
but WITHOUT ANY WARRANTY; without even the implied warranty of MERCHANTABILITY or FITNESS FOR A PARTICULAR PURPOSE. See the
GNU General Public License for more details.

You should have received a copy of the GNU General Public License along with this program. If not, see <https://www.gnu.org/licenses/>.

Also add information on how to contact you by electronic and paper mail.

If the program does terminal interaction, make it output a short
notice like this when it starts in an interactive mode:

<program> Copyright (C) <year> <name of author>
This program comes with ABSOLUTELY NO WARRANTY; for details type `show w'.

Seite 48

This is free software, and you are welcome to redistribute it
under certain conditions; type `show c' for details.

The hypothetical commands `show w' and `show c' should show the appropriate parts of the General Public License. Of course, your program's commands might be different; for a GUI interface, you would use an "about box".

You should also get your employer (if you work as a programmer) or school, if any, to sign a "copyright disclaimer" for the program, if necessary.
For more information on this, and how to apply and follow the GNU GPL, see <https://www.gnu.org/licenses/>.

The GNU General Public License does not permit incorporating your program into proprietary programs. If your program is a subroutine library, you may consider it more useful to permit linking proprietary applications with the library. If this is what you want to do, use the GNU Lesser General Public License instead of this License. But first, please read <https://www.gnu.org/licenses/why-not-lgpl.html>.

Seite 49

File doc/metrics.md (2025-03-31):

# VRS Replace - Metrics

Data logging could be handled by using a Prometheus database and afterwards analyzed with Grafana.
https://prometheus.io

grafana expample dashboard

## Configuring

Add the following lines inside your prometheus.yml configuration file. Section "scrape_configs:"

```
- job_name: 'vrsreplace'
  scrape_interval: 10s # >= Depending on your meassurement interval
  static_configs:
  - targets: ['<IP of VRS-Replace>']
    metrics_path: /metrics
```

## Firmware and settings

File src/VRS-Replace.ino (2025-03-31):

/**********************************************************************
*	Copyright (C) 2025  Martin Lange
*	This file is part of VRS Replace. OpenSource thermal solar control
*
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
*	You should have received a copy of the GNU General Public License
*	along with this program.  If not, see <https://www.gnu.org/licenses/>.
*	https://github.com/kleinekuh/vrsreplace
**********************************************************************/

/*
Version 0.9.8
*/

#include <Arduino.h>
#include <ArduinoJson.h>
#include <WiFi.h>

#include <PsychicHttp.h>
#include <TemplatePrinter.h>
#include <Update.h>

#include <U8g2lib.h>
#include <Wire.h>

#include "FS.h"
#include "SD.h"
#include "SPI.h"
#include "time.h"
#include "mqtt_client.h"


#include "config_html_gz.h"
#include "index_html_gz.h"
#include "main_css_gz.h"
#include "mainall_js_gz.h"
#include "timerformheating_html_gz.h"
#include "timerformsolarpump_html_gz.h"
#include "update_html_gz.h"


#define CONFIG_HTTPD_MAX_REQ_HDR_LEN 1024

#define VRS_VERSION "0.9.8"
#define CONVERSIONS_PER_PIN 100

#define GPIO_HEAT 16
#define GPIO_SOLAR_PUMP 17
#define GPIO_CIRCULATION_PUMP 18

#define SD_MOSI     23
#define SD_MISO     19
#define SD_SCLK     18
#define SD_CS       5


//#define DEBUGGING

#ifdef DEBUGGING
#define DEBUG_B(...) Serial.begin(__VA_ARGS__)
#define DEBUG_P(...) Serial.println(__VA_ARGS__)
#define DEBUG_C(...) Serial.print(__VA_ARGS__)
#define DEBUG_F(...) Serial.printf( __VA_ARGS__ )
#else
#define DEBUG_B(...)
#define DEBUG_P(...)
#define DEBUG_C(...)
#define DEBUG_F(...)
#endif

enum SystemStateType{
  INIT,
  FIRMWARE_CHANGE,
  RUNNING,
  REBOOT,
  ERROR,
  CONFIG,
  MQTT_CHANGE
};

enum PP_HTTP_TYPE{
  PP_GET,
  PP_POST,
  PP_GET_POST,
  PP_UPLOAD
};

enum PP_PAGE_TYPE{
  PP_JSON,
  PP_HTML,
  PP_HTML_GZ,
  PP_JS_GZ,
  PP_CSS_GZ
};

typedef struct{
  int temperatureSRT = 10000; // Refresh Time for TemperatureSensors
  int temperatureLWT = 10000; // Write Time for Temperature Log (large)
  int temperatureSWT = 60000; // Write Time for Temperature Log (small)
  int sensorAvgTemperatureCalcSize=10;
  int maxtemperature = 120; 
  char lutPath[25] = "/sensordata";
  char logPath[25] = "/log";
  char webServerPath[25] = "/webserver";
  char ssid[25] = "";
  char password[25] = "";
  char ntpserver[25] = "de.pool.ntp.org";
  int wificonnectionretries=10;
  bool wificonfigured=false;
  unsigned long wifireconnectinterval = 60000;
  bool allowcors = false;
  char dnsname[25] = "vrsreplace";
  bool deliverfromsd = false;
  bool mqttactive = false;
  char mqttserver[50] = "";
  unsigned long mqttsendinterval = 5000;
  char language[3] = "en";
  char timezone[50] = "4---CET-1CEST,M3.5.0,M10.5.0/3";
} VRSReplaceConfig;
VRSReplaceConfig config;

typedef struct{
  uint32_t previousSRTMillis=0;
  uint32_t previousLWTMillis=0;
  uint32_t previousSWTMillis=0;
  uint32_t previousMQTTMillis=0;

  volatile int nbTimers=0;
  volatile int lastLogId=0;
  volatile int datestamp=0;
  volatile int acthour=0;
  volatile bool sdmount=false;
  volatile bool sdready=false;
  volatile bool adc_conversion_started = false;
  volatile bool adc_coversion_done = false;
  volatile bool lutloaded=false;
  volatile bool mqttinited=false;
  volatile bool mqttactive=false;
  uint8_t sdCardType;
  uint64_t sdTotalBytes;
  unsigned long wifipreviousMillis = 0;
  int wificonnectionretries = 0;
  SystemStateType systemState = INIT;
  IPAddress actIP;
} VRSRunntime;
VRSRunntime runtime;

enum RCStatus{
  RC_OK = 1,
  RC_ERROR = 2
}; 

enum VRSensorType {
  VR10 = 1,
  VR11 = 2
};

enum RelaisType {
  HEAT = 1,
  SPUMP = 2,
  CPUMP = 3
};

enum TemperatureMeasurementType {
  TNONE = 0,
  SP1 = 1,
  SP2 = 2,
  AVG_SP1_SP2 = 3,
  KOL1 = 4
};

enum TimerProgramType {
  DAILY = 1,
  WEEKDAYS = 2,
  PER_REQUEST = 3,
  DYNAMIC = 4
};

enum TimerStateType {
  ON = 1,
  OFF = 2,
  WAIT = 3,
};


enum LogStatusCode{

  NOCODE = 0,

  SETUP_START = 100,
  NEW_DAY = 101,
  SYSTEM_ERROR = 110,
  SYSTEM_RESTARTED = 111,
  SYSTEM_NTP_REFRESHED = 112,
  SYSTEM_FIRMWARE_CHANGED = 113,
  SYSTEM_FIRMWARE_ERROR = 114,

  SYSTEM_ADC_DEINIT_OK = 115,
  SYSTEM_ADC_DEINIT_ERROR = 116,

  SYSTEM_CONFIG_CHANGED = 117,
  SYSTEM_CONFIG_CHANGED_RESTART = 118,
  SYSTEM_CONFIG_ERASED = 119,
  SYSTEM_CONFIG_NOT_SAVED = 120,

  NO_LUT_FILE = 121,
  NO_SDCARD = 122,

  SYSTEM_NO_WIFI = 125,
  SYSTEM_RECONNECT_WIFI = 126,
  SYSTEM_WIFI_AP_CONFIG = 127,

  TEST_GPIO_NOID = 130,
  TEST_GPIO_START = 131,
  TEST_GPIO_STOP = 132,

  TIME_SET = 180,
  TIME_NOT_SET = 181,
  TIME_SET_TIMEZONE = 182,

  TIMER_STARTED =	200,
  TIMER_STOPPED =	201,
  TIMER_WAIT = 202,
  TIMER_RESUME = 203,
  TIMERS_REMOVED =204,
  TIMERS_NOT_REMOVED = 205,
  TIMER_DELETED = 206,
  TIMER_HEAT_ADDED = 207,
  TIMER_SPUMP_ADDED = 208,
  TIMER_CPUMP_ADDED = 209,
  TIMER_HEAT_CHANGED = 210,
  TIMER_SPUMP_CHANGED = 211,
  TIMER_CPUMP_CHANGED = 212,
  
  WS_START_TIMER_NO_ID =	300,
  WS_START_TIMER_ID_NOT_FOUND =	301,
  WS_START_TIMER_ID_STARTED =	302,
  WS_START_TIMER_RELAIS_STARTED =	303,
  WS_START_TIMER_DEACTIVATED = 304,
  WS_START_TIMER_OK =	305,
  WS_STOP_TIMER_NO_ID =	306,
  WS_STOP_TIMER_OK = 307,
  WS_STOP_TIMER_NOT_RUNNING =	308,
  WS_TIMERS_DELETE_NO_ID = 309,
  WS_TIMERS_DELETE_GENERAL_ERROR = 310,
  WS_TIMERS_DELETE_OK =	311,
  WS_GET_TIMER_NO_ID = 312,
  WS_GET_TIMER_ID_NOT_FOUND = 313,
  WS_CHANGE_TIMER_NO_TIMER = 314,
  WS_CHANGE_TIMER_GENERAL_ERROR = 315,
  WS_CHANGE_TIMER_ADDED = 316,
  WS_CHANGE_TIMER_CHANGED = 317,

  WS_CLIENT_CONNECTED	= 340,
  WS_CLIENT_DISCONNECTED = 341,

  WS_FIRMWARE_UPDATE_START = 350,
  WS_FIRMWARE_UPDATE_ERROR = 351,
  WS_FIRMWARE_UPDATE_OK = 352,

  WS_CHANGE_SETUP_ERROR = 360,
  WS_CHANGE_SETUP_NO_CONFIG = 361,

  MQTT_STARTED = 370,
  MQTT_STOPPED = 371,
  MQTT_ERROR = 372,
  MQTT_INIT = 373,
  MQTT_INIT_ERROR = 374

};

enum PrioCode{
  ALL = 0,
  SYSTEM = 1,
  PRIO_HIGH = 10,
  PRIO_LESS = 12,
  PRIO_LOW = 20,
};

enum MESSAGE_PUBLISH{
    C_WS              = 1U << 0U,
    C_MQTT            = 1U << 1U,
    C_LOGFILE         = 1U << 2U,
    C_HTTP            = 1U << 3U,
    C_WS_STATUS       = 1U << 4U, 
    C_WS_TIMER        = 1U << 5U, 
    C_WS_LOG          = 1U << 6U, 
    C_WS_TEMPERATURE  = 1U << 7U,
};

// Struct for Timers / Relais
typedef struct{
  int id;                                               // Internal unique ID, used for sorting and processing
  char bez[30];                                         // Given Name of this Timer
  int gpiopin;                                          // Which ESP Pin is addressed for the Relais
  RelaisType relaistype;                                // Type of the Relais (HEAT, SPUMP -> SolarPump, CPUMP -> CirculationPump / actuall not implemented )
  int time_on;                                          // Start Time Format HH24MMSS (Relaistype HEAT)
  int time_off;                                         // End Time Format HH24MMSS (Relaistype HEAT)
  int weekdays[7];                                      // Day of Week for the Timer  (Relaistype HEAT)
  int running_period;                                   // Duration (in sec) how long the Relais is HIGH (Relaistype SPUMP)
  int waiting_period;                                   // Duration (in sec) how long the Relais is LOW (Relaistype SPUMP) -> timerstatetype = WAIT
  TimerProgramType timer_program_type;                  // Timer Programtype DAILY, WEEKDAYS, PER_REQUEST, DYNAMIC (not implemented) (Relaistype HEAT)
  int temperature_on;                                   // Start Temperature HEAT
  int temperature_off;                                  // End Temperature HEAT, SPUMP
  TemperatureMeasurementType tempmeasurementtype;       // How the temperature is meassured for this Timer (SP1, SP2 or AVG)
  int temperature_difference;                           // Temperature Differece between temp sensor KOL1 and tempmeasurementtype (Relaistype SPUMP)
  int hysteresis;                                       // Hysteresis temperature for restart HEAT Timer again, if time_off not reached
  bool active;                                          // Timer Active or Inactive
  TimerStateType timerstatetype;                        // Actual running state (ON = Relais High, Off = Relais Low, Wait = Relais Low)
  int datestamp;                                        // Datestamp. Is changing in combination with timerstatetype YYYYMMSS (volatile)
  int timestamp;                                        // Timestamp. Same as datestamp HH24MMSS (volatile)
  int runtime;                                          // How many seconds the timer has operated
  int waittime;                                         // How many seconds the timer had been in wait state
  int runnings;                                         // Number of runnings
  int waitings;                                         // Number of waitings
  int laststartdate;                                    // Last startdate YYYYYMMSS
  int laststarttime;                                    // Last starttime HH24MMSS
  int nextstarttime;                                    // Timer next starttime (for spump)
  int nextstoptime;                                     // Timer next stoptime (for spump)
  double nextstarttemp;                                 // Timer next start temperature (for hysteresis)
  double nextstoptemp;                                  // Timer next stop temperature (for hysteresis)
  bool publishhomekit;                                  // Timer visible on Homekit
  int avgtempincreasepermin;                            // Average Temperature increase per min.
} RelaisTimer;


// Struct for predefined VR-Sensor Temp calculation
typedef struct {
  VRSensorType sensorType;
  double TaMin;
  double TaMax;
  int numberofvalues;
  int** values;
} VRPreValue;
VRPreValue vrprevalues[2];

// Struct for TemperatureSensor Masurement
typedef struct {
  String bez;
  int deviceId;
  int gpiopin;
  VRSensorType sensorType;
  TemperatureMeasurementType tempmeasurementtype;
  double Ta;    // Der aktuelle Temperatur Wert
  double TaAvg; // Der kalkulierte Temperatur Mittelwert
  double TaMax; // Max Wert
  double TaMin; // Min Wert
  int counter;  // Wie oft wurde der Werte bereits ermittelt, Verwendet fuer Avg
  double TaS;   // Aufsummierter Werte fuer Avg
  int* lut = (int*)malloc(4096 * sizeof(int));
} TemperatureSensor;
TemperatureSensor temperaturesensors[3];

typedef struct{
  int deviceid;
  String bez;
  double TaMax[24] = {0};
  double TaMin[24] = {0};
  double TaMaxY[24] = {0};
  double TaMinY[24] = {0};
} TemperaturePerHour;
TemperaturePerHour temperatureperhours[3];

typedef struct{
  int id;
  PrioCode priocode;
  int date;
  int time;
  LogStatusCode code;
  char message[100]={'\0'};
} StatusLog;

struct tm tm;
bool timeset=false;

const char* apssid     = "VRS-Replace";
const char* appassword = "12345678";

RelaisTimer* timers;

void setup() {

  heap_caps_malloc_extmem_enable(512);

  Serial.begin(115200);
  setupSDCard();

 
  u8g2_prepare();
  displayBoot(config.ssid, 0);

  readConfig();
  initSystemLog();
  
  WiFi.setHostname(config.dnsname);
  WiFi.setAutoReconnect(false);
  WiFi.persistent(false);
  
  if(!config.wificonfigured){
    WiFi.softAP(apssid, appassword);
    delay(500);
    runtime.actIP = WiFi.softAPIP();
    DEBUG_F("\nStarting AP Mode: %s", runtime.actIP.toString(false).c_str());
    publishLogMessage(C_LOGFILE, NULL, -1, RC_OK, SYSTEM_WIFI_AP_CONFIG, runtime.actIP.toString(false).c_str());
    runtime.systemState = CONFIG;
  }else{
    int x=0;
    WiFi.begin(config.ssid, config.password);
    while (WiFi.status() != WL_CONNECTED && x<config.wificonnectionretries) {
      delay(1000);
      x++;
      displayBoot(config.ssid, x);
      DEBUG_F("\nNo Connection: %s %d", config.ssid, x);
    }
    if(!WiFi.isConnected()){
      config.wificonfigured = false;
      writeConfig();
      delay(1000);
      runtime.systemState = CONFIG;
      ESP.restart();
      return; 
    }else{
      runtime.actIP = WiFi.localIP();
      DEBUG_F("\nStarting ST Mode: %s", runtime.actIP.toString().c_str());
      timeset = initTime();
      if(timeset)runtime.acthour = getHour();
      runtime.systemState = RUNNING;
    }
  }

  addServerFunctions();

  if(runtime.systemState==RUNNING){
    reloadTimers();
    initTemperatureSensors();
    initTempsensorLog();
    publishLogMessage(C_LOGFILE, NULL, -1, RC_OK, SETUP_START, runtime.actIP.toString(false).c_str());

    pinMode(GPIO_HEAT, OUTPUT);
    pinMode(GPIO_SOLAR_PUMP, OUTPUT);
    
    if(config.mqttactive){
      initMQTT();
      startMQTT(); 
    } 
  }

  runtime.previousSRTMillis = millis();
  runtime.previousLWTMillis = runtime.previousSRTMillis;
  runtime.previousSWTMillis = runtime.previousSRTMillis;

}

void loop() {
  unsigned long currentMillis = millis();

  
  switch(runtime.systemState){
    
    case INIT: break;
    case FIRMWARE_CHANGE: 
      if(runtime.adc_conversion_started){
        stopAllTimers();
        if(!deinitTemperatureSensors()){
          publishLogMessage(C_LOGFILE, NULL, -1, RC_ERROR, SYSTEM_ADC_DEINIT_ERROR, NULL);
        }else{
          publishLogMessage(C_LOGFILE, NULL, -1, RC_OK, SYSTEM_ADC_DEINIT_OK, NULL);
        }
      }
      stopMQTT();
    break;
    case RUNNING:
      if(runtime.datestamp==0) runtime.datestamp = dateStamp();
      else if(runtime.datestamp != dateStamp()){
        publishLogMessage(C_LOGFILE, NULL, -1, RC_OK, NEW_DAY, NULL);
        runtime.systemState = REBOOT;
        break;
      }
      if(!checkSD()){
        stopAllTimers();
      }else{
        if (runtime.adc_coversion_done == true) {
          processTemperature();
          runtime.adc_coversion_done = false;
        }
        processTimers();
        if(currentMillis - runtime.previousLWTMillis >= config.temperatureLWT){
          writeTemperatureLog();
          runtime.previousLWTMillis = currentMillis;
        }
        if(currentMillis - runtime.previousSRTMillis >= config.temperatureSRT){
          publishLogMessage(C_WS | C_WS_STATUS | C_WS_TEMPERATURE , NULL, -1, RC_OK, NOCODE, NULL);
          runtime.previousSRTMillis = currentMillis;
        }
        if(currentMillis - runtime.previousSWTMillis >= config.temperatureSWT){
          writeHourlyTemperatureLog();
          runtime.previousSWTMillis = currentMillis;
        }
        if(runtime.mqttactive && currentMillis - runtime.previousMQTTMillis >= config.mqttsendinterval){
          sendMQTTMessages();
          runtime.previousMQTTMillis = currentMillis;
        }
        displayRunning();
      }
      
    break;
    case MQTT_CHANGE:
      if(config.mqttactive){
        startMQTT();
      }else{
        stopMQTT();
      }
      DEBUG_F("\nMQTT Change %d", config.mqttactive);
      runtime.systemState = RUNNING;
    break;
    case REBOOT: 
      displayReboot();
      delay(2000);
      stopAllTimers();
      if (runtime.adc_coversion_done == true) {
          processTemperature();
      }
      writeHourlyTemperatureLog();
      writeTemperatureLog();
      deinitTemperatureSensors();
      delay(1000);
      ESP.restart();
    break;
    case ERROR: 
      displayError();
      break;
    case CONFIG: 
      displayConfig();
    break;
     
  }

  if (runtime.systemState == RUNNING)checkWifi();
  delay(1000);
}

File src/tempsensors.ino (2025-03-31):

/**********************************************************************
*	Copyright (C) 2025  Martin Lange
*	This file is part of VRS Replace. OpenSource thermal solar control
*
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
*	You should have received a copy of the GNU General Public License
*	along with this program.  If not, see <https://www.gnu.org/licenses/>.
*	https://github.com/kleinekuh/vrsreplace
**********************************************************************/

/*
Version 0.9.8
*/

uint8_t vrprevalues_count;
uint8_t tempsensors_count;
uint8_t *adc_pins;
uint8_t adc_pins_count;
adc_continuous_data_t* result = NULL;

void ARDUINO_ISR_ATTR adcComplete() {
  runtime.adc_coversion_done = true;
}

void initTemperatureSensors(){
  
  vrprevalues[0] = initVRPreValue(VR10, 0, 120, String(config.lutPath) + "/vrs10.txt");
  vrprevalues[1] = initVRPreValue(VR11, -20, 130, String(config.lutPath) + "/vrs11.txt");
  vrprevalues_count = sizeof(vrprevalues)/sizeof(vrprevalues[0]);

  temperaturesensors[0] = buildSensor(1, "Kol1", 36, VR11, KOL1, String(config.lutPath) + "/lut36.txt");
  temperaturesensors[1] = buildSensor(2, "Sp1", 39, VR10, SP1, String(config.lutPath) + "/lut39.txt");
  temperaturesensors[2] = buildSensor(3, "Sp2", 34, VR10, SP2, String(config.lutPath) + "/lut34.txt");

  tempsensors_count = sizeof(temperaturesensors)/sizeof(temperaturesensors[0]);
  adc_pins_count = tempsensors_count;
  adc_pins = (uint8_t*)malloc(adc_pins_count * sizeof(uint8_t));
  for(int i=0;i<adc_pins_count;i++) adc_pins[i] = temperaturesensors[i].gpiopin;

  analogContinuousSetWidth(12);
  analogContinuousSetAtten(ADC_11db);
  analogContinuous(adc_pins, adc_pins_count, CONVERSIONS_PER_PIN, 800000, &adcComplete);

  analogContinuousStart();
  runtime.adc_conversion_started = true;
}

bool deinitTemperatureSensors(){
  if(!runtime.adc_conversion_started) return true;
  if(!analogContinuousStop()) return false;
  delay(100);
  if(!analogContinuousDeinit()) return false;
  runtime.adc_conversion_started = false;
  return true;
}

TemperatureSensor buildSensor(int deviceId, String bez, int gpiopin, VRSensorType sensorType, TemperatureMeasurementType tempmeasurementtype, String lutName) {
  TemperatureSensor rc;
  rc.bez = bez;
  rc.deviceId = deviceId;
  rc.gpiopin = gpiopin;
  rc.sensorType = sensorType;
  rc.tempmeasurementtype = tempmeasurementtype;
  rc.Ta = 0.0;
  rc.TaMax = 0.0;
  rc.TaMin = 0.0;
  rc.counter=-1;
  rc.TaS = 0.0;
  readLutFileToIntArray(lutName.c_str(), rc.lut);
  pinMode(rc.gpiopin, INPUT);

  return rc;
}

VRPreValue initVRPreValue(VRSensorType sensorType, double TaMin, double TaMax, String lutName){

  VRPreValue vrprevalue;
  vrprevalue.sensorType = sensorType;
  vrprevalue.TaMin = TaMin;
  vrprevalue.TaMax = TaMax;
  vrprevalue.numberofvalues = getNumberOfLutEntries(lutName.c_str());

  int* temparray = (int*)malloc(vrprevalue.numberofvalues * sizeof(int));
  readLutFileToIntArray(lutName.c_str(), temparray);
  
  vrprevalue.numberofvalues = vrprevalue.numberofvalues/2;
  vrprevalue.values = (int**)malloc(vrprevalue.numberofvalues * sizeof(int));
  for (int i = 0; i < vrprevalue.numberofvalues; i++) vrprevalue.values[i] = (int*)malloc(2 * sizeof(int));

  int j=0;
  for(int i=0;i<vrprevalue.numberofvalues;i++){
      vrprevalue.values[i][0] = temparray[j++];
      vrprevalue.values[i][1] = temparray[j++];
  }
  free(temparray);
  return vrprevalue;
}

double calcTempFromPreValues(int value, VRPreValue vrprevalue){
  int x1, x2;
  int y1, y2;
  if(value==0) return vrprevalue.values[vrprevalue.numberofvalues-1][1];

  for(int i=0;i<vrprevalue.numberofvalues;i++){
    //DEBUG_F("%d %d %d\n", value, vrprevalue.values[i][0], vrprevalue.values[i][1]);
    if(value==vrprevalue.values[i][0]) {
      return vrprevalue.values[i][1];
    }
    if(value>vrprevalue.values[i][0]){
      x2=vrprevalue.values[i][0];
      y2=vrprevalue.values[i][1];
      if(i>0){
        x1=vrprevalue.values[i-1][0];
        y1=vrprevalue.values[i-1][1];
      }else{
        return vrprevalue.values[0][1];
      }
      i=1000;
    }
  }
  //DEBUG_F("x2=%d, y2=%d, x1=%d, y1=%d\n", x2, y2, x1, y1);
  double d1 = ((double)(y2-y1))/((double)(x2-x1));
  double calcTemp = y1+(d1*(value-x1));
  //DEBUG_F("calcTemp %lf %lf\n", d1, calcTemp);
  return calcTemp;
}

void processTemperature(){
  if (analogContinuousRead(&result, 0)) {
      analogContinuousStop();

      int hour = getHour();

      for (int i = 0; i < adc_pins_count; i++) {
        int adc = result[i].avg_read_raw;
        int pin = result[i].pin;

        int tempsensor_pos = getTemperaturSensorPosFromPin(pin);
        int vrdefvalue_pos = -1;
        if(tempsensor_pos!=-1){
          vrdefvalue_pos = getVRPreValuesPosFromVRSensorType(temperaturesensors[tempsensor_pos].sensorType);
        }
        if(vrdefvalue_pos!=-1){
          adc = temperaturesensors[tempsensor_pos].lut[adc];
          double calcTemp = calcTempFromPreValues(adc, vrprevalues[vrdefvalue_pos]); 
          if(calcTemp<=-20 || calcTemp>=130) calcTemp=0;
          if(calcTemp <= vrprevalues[vrdefvalue_pos].TaMin || calcTemp >= vrprevalues[vrdefvalue_pos].TaMax){
            calcTemperature(calcTemp, tempsensor_pos, hour, false);
          }else{
            calcTemperature(calcTemp, tempsensor_pos, hour, true);
          }
        }
      }
      runtime.acthour=hour;
      analogContinuousStart();
  }
}

void calcTemperature(double temperature, int pos, int hour, bool storeminmax){
  
  if(temperaturesensors[pos].counter==-1){
    temperaturesensors[pos].Ta = temperature;
    temperaturesensors[pos].TaS = temperature;
    temperaturesensors[pos].TaAvg = temperature;
    temperaturesensors[pos].counter=0;
    temperaturesensors[pos].TaMin = 130;
    temperaturesensors[pos].TaMax = -20;
  }

  if(temperaturesensors[pos].counter>=config.sensorAvgTemperatureCalcSize){
    temperaturesensors[pos].TaAvg = (temperaturesensors[pos].TaS / temperaturesensors[pos].counter);
    temperaturesensors[pos].TaS = 0.0;
    temperaturesensors[pos].counter=0.0;
  }

  temperaturesensors[pos].TaS = temperaturesensors[pos].TaS + temperature;
  temperaturesensors[pos].counter++;

  temperaturesensors[pos].Ta = temperature;
  if(storeminmax){
    if(hour!=runtime.acthour){
      temperaturesensors[pos].TaMax=temperature;
      temperaturesensors[pos].TaMin=temperature;
      temperatureperhours[pos].TaMax[hour] = temperature;
      temperatureperhours[pos].TaMin[hour] = temperature;
    }else{
      if(temperature > temperaturesensors[pos].TaMax)  temperaturesensors[pos].TaMax=temperature;
      if(temperature < temperaturesensors[pos].TaMin)  temperaturesensors[pos].TaMin=temperature;
      if(temperature > temperatureperhours[pos].TaMax[hour]) temperatureperhours[pos].TaMax[hour] = temperature;
      if(temperature < temperatureperhours[pos].TaMin[hour]) temperatureperhours[pos].TaMin[hour] = temperature;
    }
  }

}
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

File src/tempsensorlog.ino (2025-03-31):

/**********************************************************************
*	Copyright (C) 2025  Martin Lange
*	This file is part of VRS Replace. OpenSource thermal solar control
*
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
*	You should have received a copy of the GNU General Public License
*	along with this program.  If not, see <https://www.gnu.org/licenses/>.
*	https://github.com/kleinekuh/vrsreplace
**********************************************************************/

/*
Version 0.9.8
*/

void initTempsensorLog(){
  readHourlyTemperatureLog(true);
}

void readHourlyTemperatureLog(bool withYesterday){
  if(!runtime.sdready) return;
  String datum = String(dateStamp());

  String fileName = String(config.logPath) + "/" + datum +"_small.csv";
  String fileNameBac = String(config.logPath) + "/" + datum +"_small_bac.csv";
  if(SD.exists(fileNameBac)){
    fileName = fileNameBac;
  }
  
  if(SD.exists(fileName)){
    File file = SD.open(fileName, FILE_READ);
    int i=0;
    while (file.available()) {
      String line = file.readStringUntil('\n');
      int x=0;      
      for(int j=1;j<25;j++){
        temperatureperhours[i].TaMax[x] = getValue(line, ',', j).toDouble();
        x++;
      }
      x=0;
      for(int j=25;j<49;j++){
        temperatureperhours[i].TaMin[x] = getValue(line, ',', j).toDouble();
        x++;
      } 
      i++;
    }
    file.close();
  } 

  if(withYesterday){
    String fileNameY = String(config.logPath) + "/" + String(dateStampYesterday()) +"_small.csv";
    if(SD.exists(fileNameY)){
      File file = SD.open(fileNameY, FILE_READ);
      int i=0;
      while (file.available()) {
        String line = file.readStringUntil('\n');
        int x=0;      
        for(int j=1;j<25;j++){
          temperatureperhours[i].TaMaxY[x] = getValue(line, ',', j).toDouble();
          x++;
        }
        x=0;
        for(int j=25;j<49;j++){
          temperatureperhours[i].TaMinY[x] = getValue(line, ',', j).toDouble();
          x++;
        } 
        i++;
      }
      file.close();
    }    
  }



}

void writeHourlyTemperatureLog(){
  
  char datebuf[9];
  char timebuf[7];
  if(!runtime.sdready) return;
  getDateTime(datebuf, timebuf);
  String fileName = String(config.logPath) + "/" + String(datebuf) +"_small.csv";
  String fileNameBac = String(config.logPath) + "/" + String(datebuf) +"_small_bac.csv";
  if(SD.exists(fileNameBac)){
    SD.remove(fileNameBac);  
  }
  if(SD.exists(fileName)){
    SD.rename(fileName, fileNameBac);
  } 
  File file = SD.open(fileName, FILE_WRITE);
  if(!file){
    DEBUG_F("writeHourlyTemperatureLog TemperatureLogFile not ready %s\n", fileName);
    return;
  }

  for(int i=0;i<3;i++){
    file.printf("%d", i);
    for(int j=0;j<24;j++){
      file.printf(",%f", temperatureperhours[i].TaMax[j]);
    }
    for(int j=0;j<24;j++){
      file.printf(",%f", temperatureperhours[i].TaMin[j]);
    }
    file.printf("\n");
  }

  file.flush();
  file.close();
  if(SD.exists(fileNameBac)){
    SD.remove(fileNameBac);  
  }


}

void writeTemperatureLog(){

  char datebuf[9];
  char timebuf[7];
  if(!runtime.sdready) return;
  getDateTime(datebuf, timebuf);
  String fileName = String(config.logPath) + "/" + String(datebuf) +"_full.csv";
  File file = SD.open(fileName, FILE_APPEND);
  if(!file){
    DEBUG_F("writeTemperatureLog TemperatureLogFile not ready %s\n", fileName);
    return;
  }

  int idH = getActiveTimerByRelaisType(HEAT);
  int idS = getActiveTimerByRelaisType(SPUMP);
  int idC = getActiveTimerByRelaisType(CPUMP);

  for(int i=0;i<3;i++){
    file.printf("%d,%s,", atoi(datebuf), timebuf);
    file.printf("%d,%d,%d,", idH, idS, idC);
    file.printf("%s,", temperaturesensors[i].bez);
    file.printf("%d,", temperaturesensors[i].deviceId);
    file.printf("%f,%f,%f\n", temperaturesensors[i].Ta, temperaturesensors[i].TaMax, temperaturesensors[i].TaMin);
  }
  file.flush();
  file.close();

}

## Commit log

2025-01-24 add sensordata and webserver htmls
2025-01-27 Bugfix
    Changed waiting delay inside loop() to 1000ms. Otherwise scheduled timerprogram’s will stop direct after start.
    [VRS-Replace.ino]
2025-07-03 PDF Description and KiCad File
    Added general description german and KiCad Layout
    [vrs_replacement.kicad_sch]
